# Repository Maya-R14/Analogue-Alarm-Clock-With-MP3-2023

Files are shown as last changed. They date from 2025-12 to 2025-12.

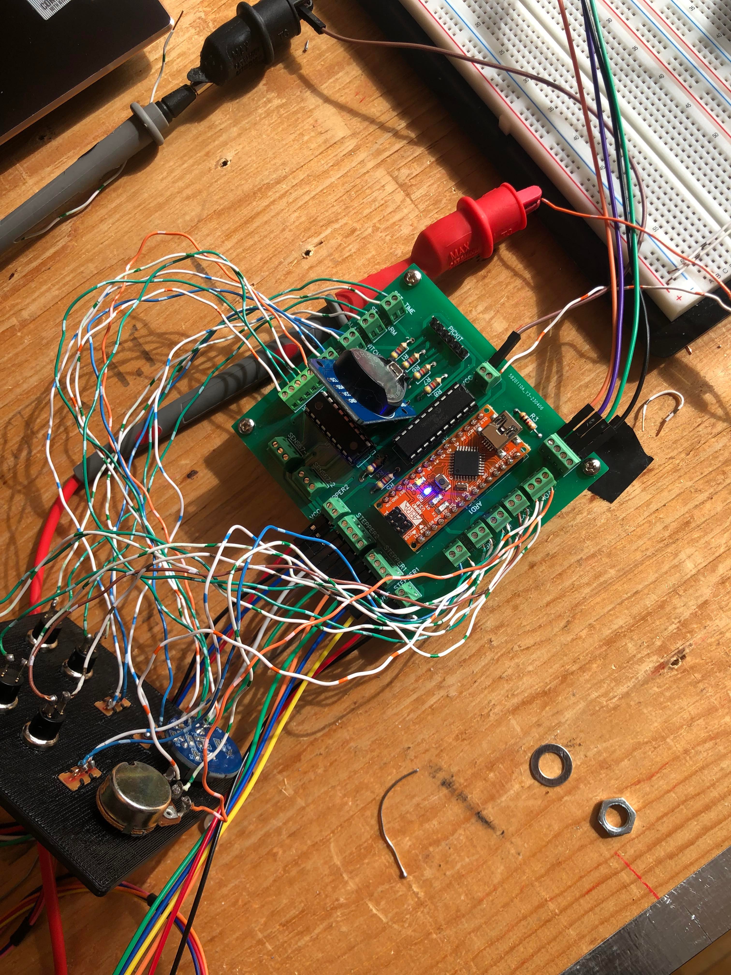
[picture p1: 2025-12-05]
Media/Testing with PCB.jpg

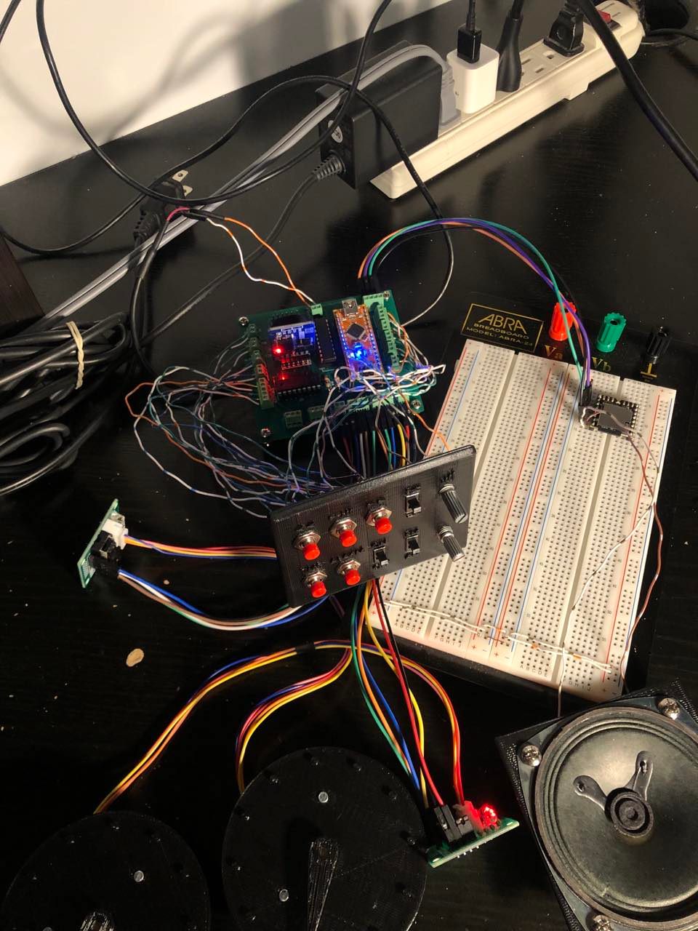
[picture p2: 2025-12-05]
Media/Testing with PCB and Faceplate.jpg

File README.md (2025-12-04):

# Analogue-Alarm-Clock-With-MP3-2023
An analog clock driven by DC motors, integrated with an MP3 playback module, combining mechanical control and embedded electronics.

## Features
- DC motor–driven clock hands for precise movement
- Integrated MP3 module for alarms or notifications
- Custom PCB for motor and module integration

## Hardware
- DC motors for clock hands
- MP3 module
- RTC module (I2C Communication)
- Microcontroller (PIC and Arduino)
- Motor drivers
- Speaker
- PCB, resistors, capacitors

## Software / Tools
- Arduino IDE (C/C++)
- DipTrace
- Salea Logic 2
- 3D Printing/Solidworks
- Laser Engraver

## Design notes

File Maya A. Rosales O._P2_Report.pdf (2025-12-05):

John Abbott College

Engineering Technologies Department

Name/Team Names:

Maya A. Rosales O.

Project 2

Technical Report

Title: Analog Clock with MP3 Player

Instructor: Hana Chammas

Date: May 27, 2023

Winter 2023

## Contents

Introduction___________________________________________________________________2

Problem Description____________________________________________________________2

Proposed Solution______________________________________________________________2

Product Development___________________________________________________________3

Technical Product Description___________________________________________________10

Operation______________________________________________________________10

Maintenance___________________________________________________________11

Troubleshooting________________________________________________________12

Lessons Learned______________________________________________________________ 13

Final OPPM_________________________________________________________________ 14

References___________________________________________________________________15

Acknowledgement and Credits___________________________________________________15

Appendix____________________________________________________________________15

A1. Bill of Materials_____________________________________________________15

A2. Media_____________________________________________________________16

A3. Engineering and Manufacturing Documentation____________________________17

A4. Miscellaneous_______________________________________________________17

## Introduction

For my project 2, I set out to build an analog clock that plays music. In this document, I will go into lengthy detail about the problem that I was trying to solve, the solution I came up with, and the steps I took to reach that solution.

I also describe in detail the process of building the clock, along with how to use it.

I wanted the clock to be aesthetically pleasing and intuitive to use and this is a philosophy I kept in mind while working on my project.

All the relevant files along with the bill of materials are also available in the index section of this document.

I would like to thank Nic the technician once again for all his help and support while working on this project.

## Problem Description

With modern phones, most people have alarms at the palm of their hands, the issue with this is that phones can fail for a number or reasons. It can range from simply forgetting to charge one’s battery, to it getting stolen, software malfunction, busted speak, etc. Having a separate dedicated time keeping/alarm device would allow for a better peace of mind and could make nice décor piece, enhancing the appearance of a room.

Most people are also woken up by blaring and disruptive alarm sounds. Although this does the job, it is rather unpleasant and, wouldn’t a person prefer to wake up to the sound of their favorite song?

## Proposed Solution

My proposal is to build an analog clock so that a user can upload their own tracks to play when the alarm goes off. The tracks will play in either a predefined sequence or at random, as selected by the user via an interface on the analog clock.

The reason it’s analog as opposed to digital is that analog adds a certain aesthetic element to the project that a digital clock doesn’t.

Alternatives:

Radio alarms have been around for a very long time, although this doesn’t allow the user to choose the music being played.

There are also light alarms, which instead of playing a sound, will use a light source to attempt to wake up the person. This is an interesting alternative, as most of these alarms claim to have health benefits over regular sound alarms. The issue with this is that the science behind it remains contentious as best. Not only that, but most of these alarms can be rather expensive.

The pros and cons of using a phone have been discussed in the previous section.

## Product Development

From the beginning, the idea was to create two separate systems for the clock, the “clock”, which would be handled by the PIC16F690 and the MP3 Player, which would be handled by an Arduino. The idea of creating two separate systems instead of one was so that they could operate independent of each other. This allows the user to listen to music using the MP3 player without disrupting the clock functionalities. Each microcontroller can “focus” on what it’s good at.

After this, I moved on to the electrical and mechanical aspect of the clock. For the electrical, I designed a schematic and PCB board using Diptrace. I then converted the PCB into Gerber files which I then sent to JLCPCB to print into a board.

The mechanical aspect involved 3D modeling the gear system and the case. After this was done, pieces were 3D printed and assembled. The front plate and the needles were laser cut and engraved.

Clock & Alarm

I’d like to preface by saying that a huge chunk of the time dedicated to this project was spent coding the PIC16F690. This is because no relevant libraries of code were readily available. Therefore, all the code for the clock and alarm was written from scratch.

With the understanding that two stepper motors would be used to move the needles, a rotary encoder to control the motors, an RTC module to keep track of the time and a handful of switches and buttons as UI, these components were bought from the very beginning, allowing for prototyping to begin.

Very early in development, it was made very obvious that the microchip did not have enough pins for all the I/O’s that were required. This prompted the purchase of the MCP23008 I/O port expander.

The code works as follows:

On power up, the microcontroller will enable all the ports as inputs, enable I2C communication, turn the alarm off (if the alarm switch is on, the alarm will be turned on anyways) and move the hands to the 0 position.

The first think the code does once it has been initialized is to check if any buttons have been pressed. The “Buttons()” function is called, which checks if the Time button, Alarm button or Alarm switch have been toggled.

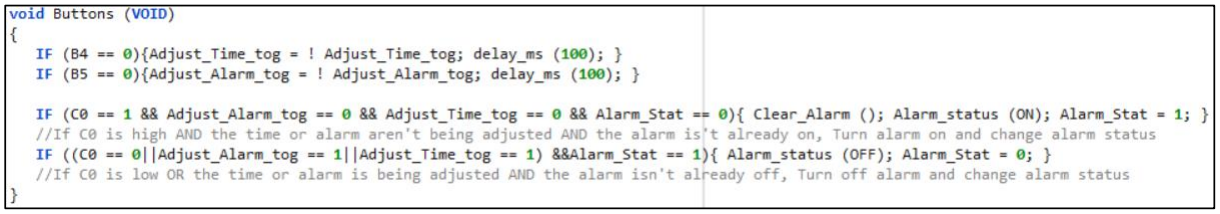
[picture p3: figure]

Once this is done, the code has three branches. Adjust time, Adjust Alarm and Display time. Since, in theory, the DS3231 already has the proper time stored, the clock will initialize on “Display time mode.”

Display time

The display time function
first fetches the time
(minutes) from the DS3231
and stores the value in
Time_min. Minutes are then converted to steps and the stepper is moved into
positions. Although the
stepper requires 2048 steps to make a full rotation,
Minutes advance in 34 steps increments (60 mins = 2040 steps). This is because the microcontroller is unable to handle decimals and to get a an exact 2048, each min
would have to be 34.13333
steps. To compensate for
this the last step has an
additional 8 steps.

The hours needle works in a

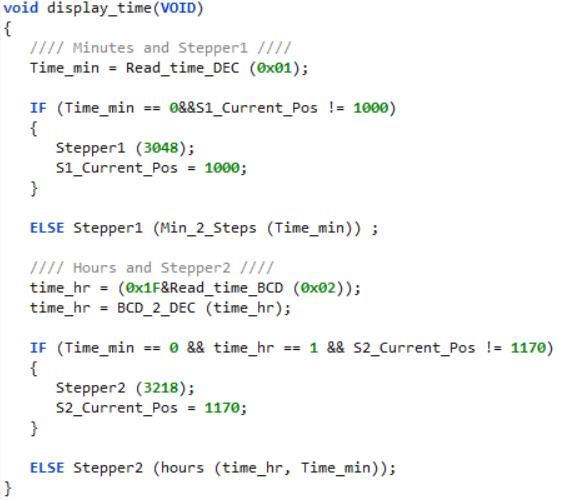
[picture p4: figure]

similar manner. It fetches the time (hours) from the DS2321 and stores the value into Time_hr. It masks the first 3 bits as they contain information that is not relevant and then converts it into decimal. Hours increase in 170 step increments. The hours needle also moves slightly closer to the next hour as minutes increase. This is done to simulate an analog clock. For every 6 mins, the clock will move 17 steps. Once again, the hour of the clock has an additional 8 steps to compensate.

Adjust time

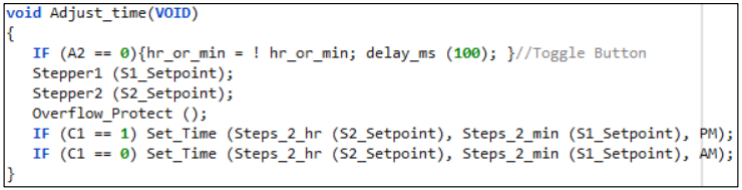
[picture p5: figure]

The adjust time function first enables interrupts to allow control of the motors through the rotary encoder. After this, it will check if the built in button on the rotary encoder has been pressed. This button allows the user to toggle between motors. After this, the two steppers will be moved into the new position.

The “Overflow_Protect” function serves to keep the position value of the motors within the expected range. The code is designed under the assumption that motor is within 0-2048 steps. If the motor is outside this range, it will replace the position value with an equivalent position value. If the motor goes to step 2148, It will move to position 2148 and replace the position with 100 (2148 - 2048 = 100).

Finally, the new position will be converted into time and the DS3231 will be updated. Whether the time is AM or PM is determined by the position of the AM/PM switch.

Adjust Alarm

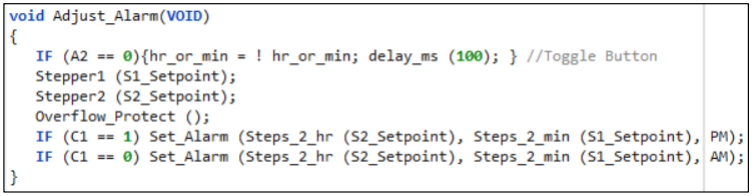
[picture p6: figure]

The adjust alarm function operates the same the adjust time function does, but instead of updating the time register in the DS3231, it updates its alarm register.

Lastly, the code will check if the alarm has gone off and if so, it will clear the alarm to allow for the next time I needs to go off.

The main function looks as shown bellow, the full code along with the relevant header files are available in the manufacturing section of this document.

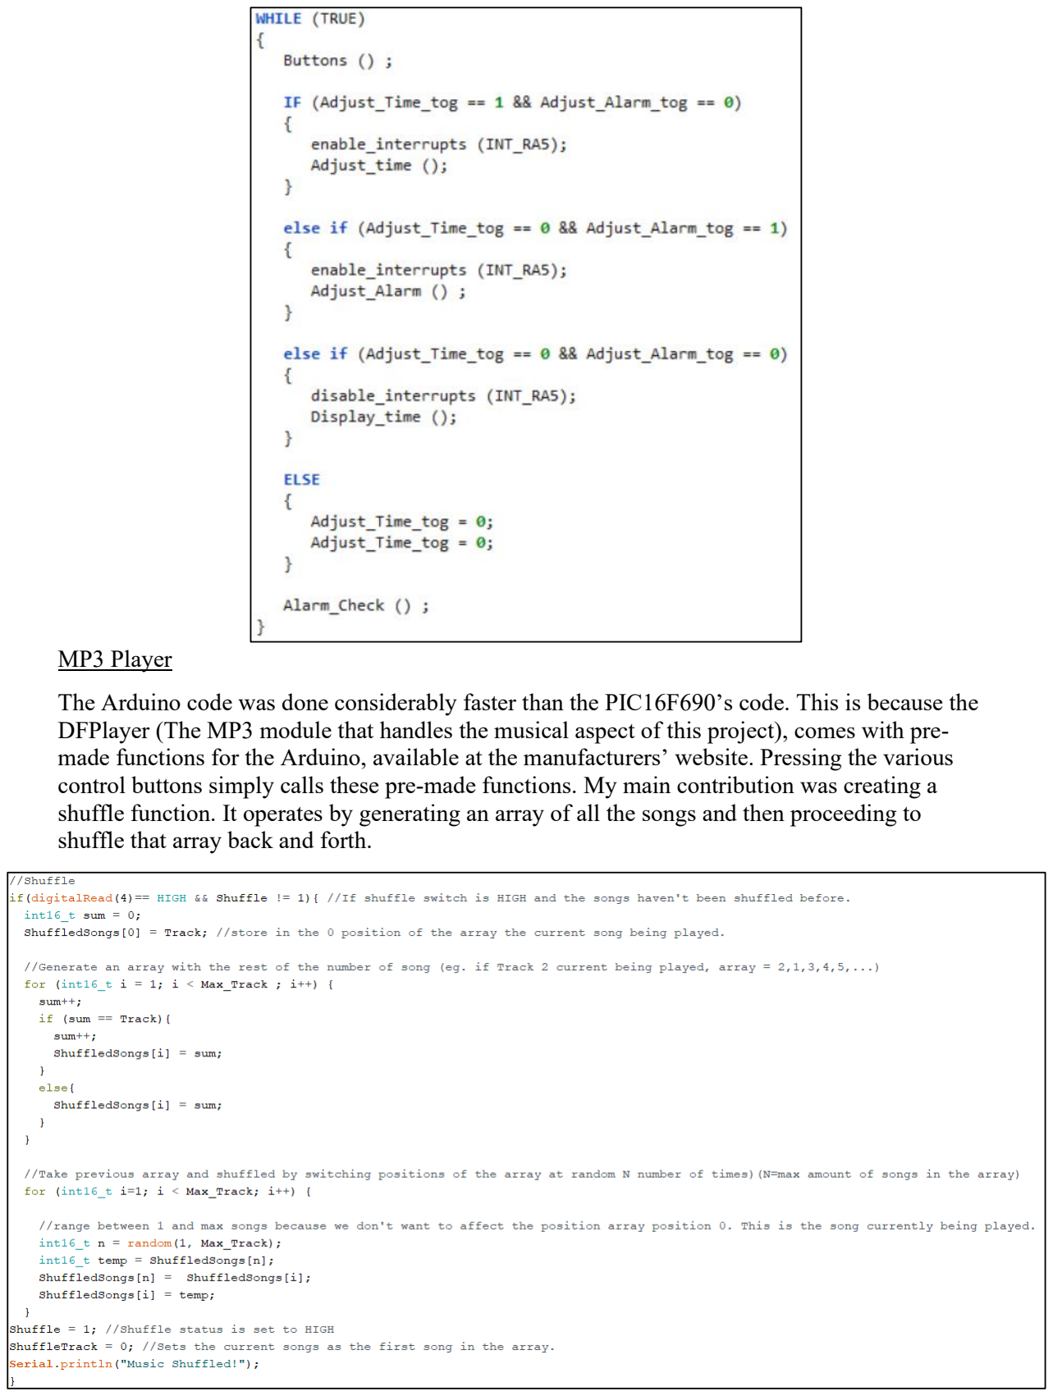
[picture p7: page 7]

MP3 Player

The Arduino code was done considerably faster than the PIC16F690’s code. This is because the DFPlayer (The MP3 module that handles the musical aspect of this project), comes with pre-made functions for the Arduino, available at the manufacturers’ website. Pressing the various control buttons simply calls these pre-made functions. My main contribution was creating a shuffle function. It operates by generating an array of all the songs and then proceeding to shuffle that array back and forth.

Schematics and Board

After fully coding the project and having a working prototype, I moved on to creating a compact PCB board for all the components. Although the electrical aspect of this project is not exceedingly complex, creating a schematic and a board is still crucial as there are several connections on the board and multiple inputs and outputs. Attempting to create a simple board from a prototype PCB would be excruciatingly hard. This is why once I had a schematic and a PCB board design, I sent it out to print with JLCPCB. The schematic and the PCB are as shown bellow and the files are available in the manufacturing section of this document.

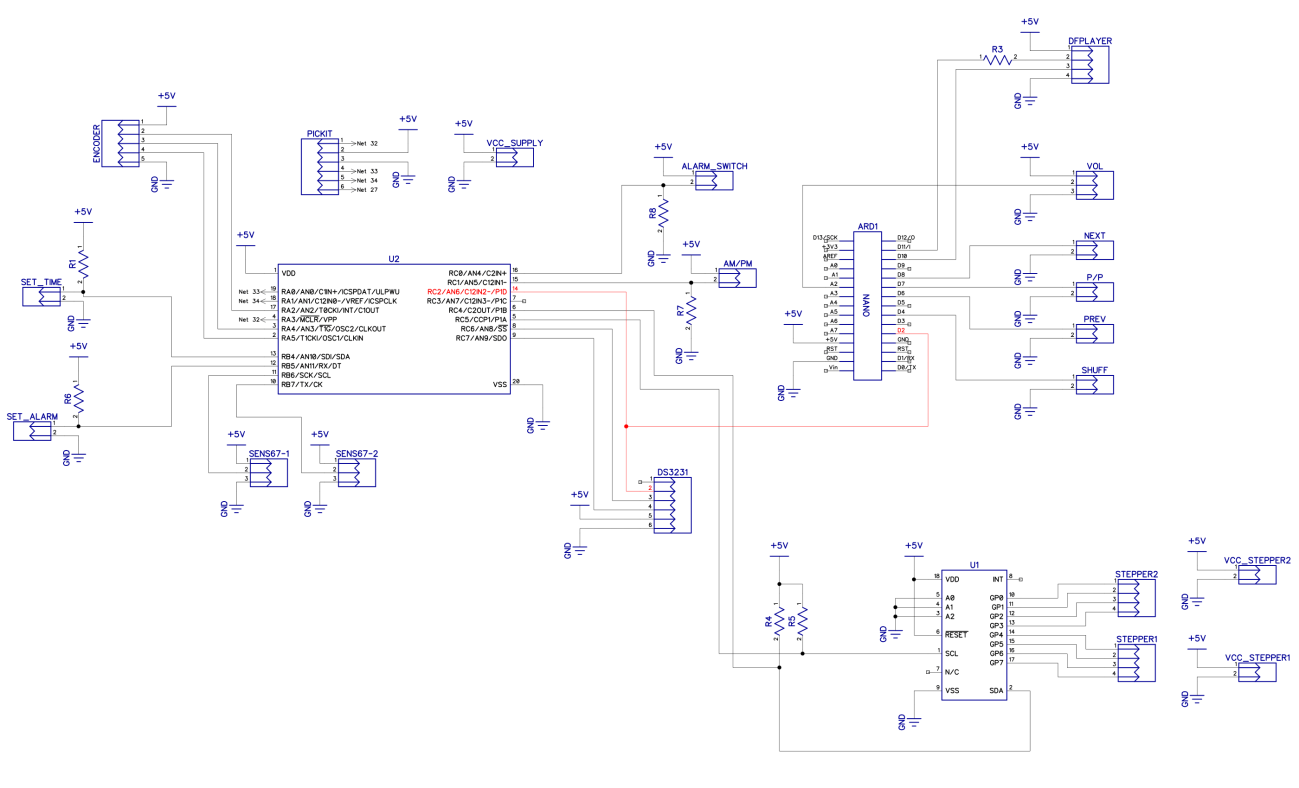
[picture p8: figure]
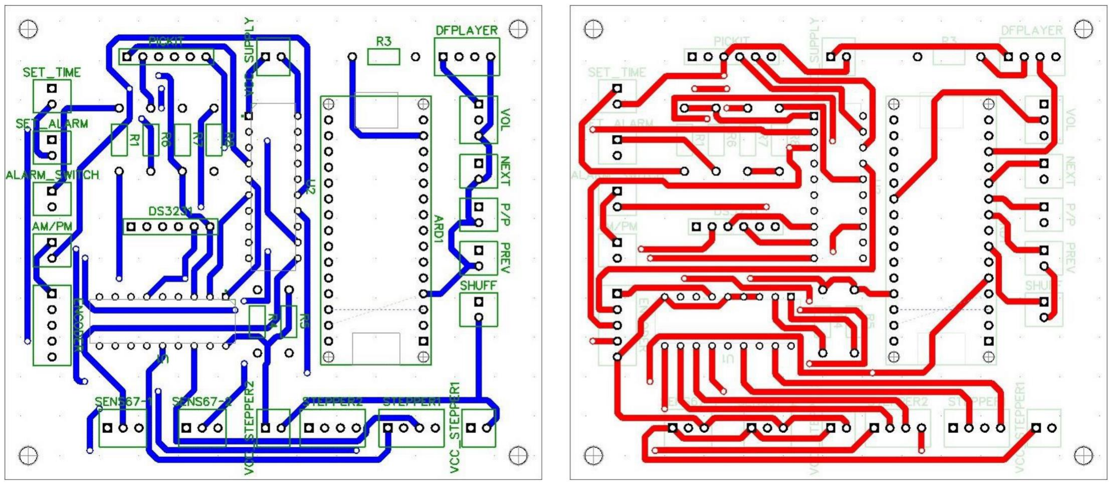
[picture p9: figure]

Gearbox

After handling the software and electrical aspects of the project. The mechanical aspect came into focus. Clocks generally have concentric shafts. Each one controlling a single needle. The goal was to recreate this system using the motors that I had in hand. The “gearbox” as shown bellow was conceived.

Each gear has 32 teeth. 32 being a divisor of 2048 which is the total amount of steps for a full revolution.

On both of the gears that function as shafts, there is a small whole near the edge of the gear. Inside this whole there’s a magnet glued. This is because there is a hall sensor module that hovers slightly above the gear. This sensor is used to determine the house position of the needles. On power up, the gears will rotate CCW until the magnet is detected and the home position is reached.

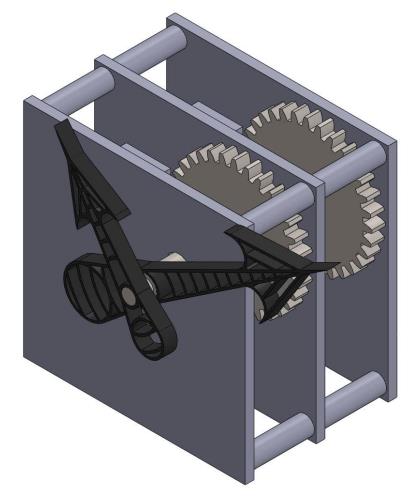
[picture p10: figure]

Case

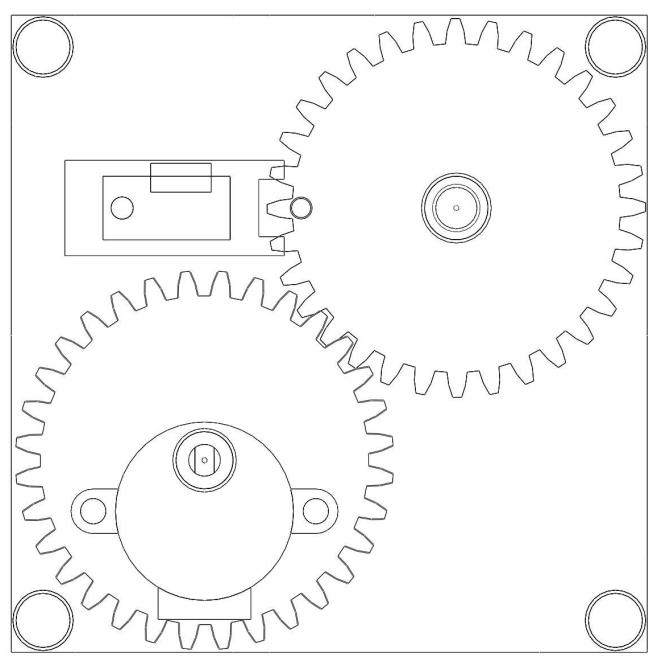
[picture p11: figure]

After this, the design of the case was rather simple. It simply had to be designed to fit the components and the gear box at the same time. Having a 3D model made of solid works with all the necessary references took out all the guesswork from this. The final look of the case is as shown bellow. Although because of its size, it had to be printed in two parts and then glued together. The face plate and the needles were then laser cut and engraved at the Pierrefonds library.

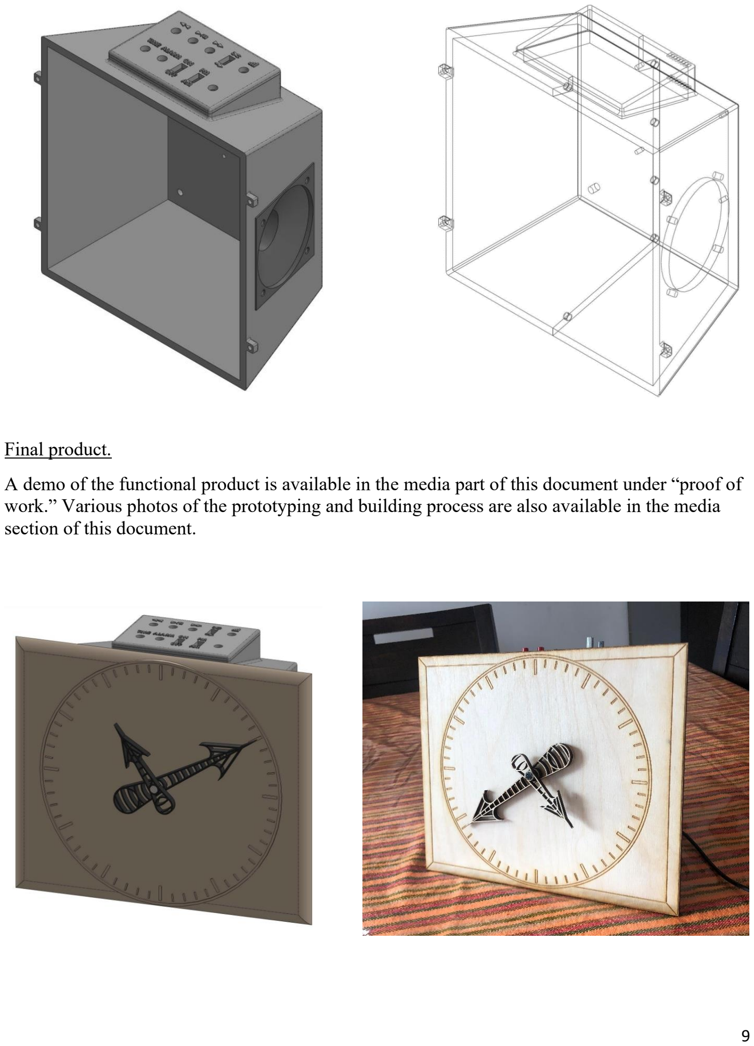
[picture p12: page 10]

Final product.

A demo of the functional product is available in the media part of this document under “proof of work.” Various photos of the prototyping and building process are also available in the media section of this document.

## Technical Product Description

## Operation

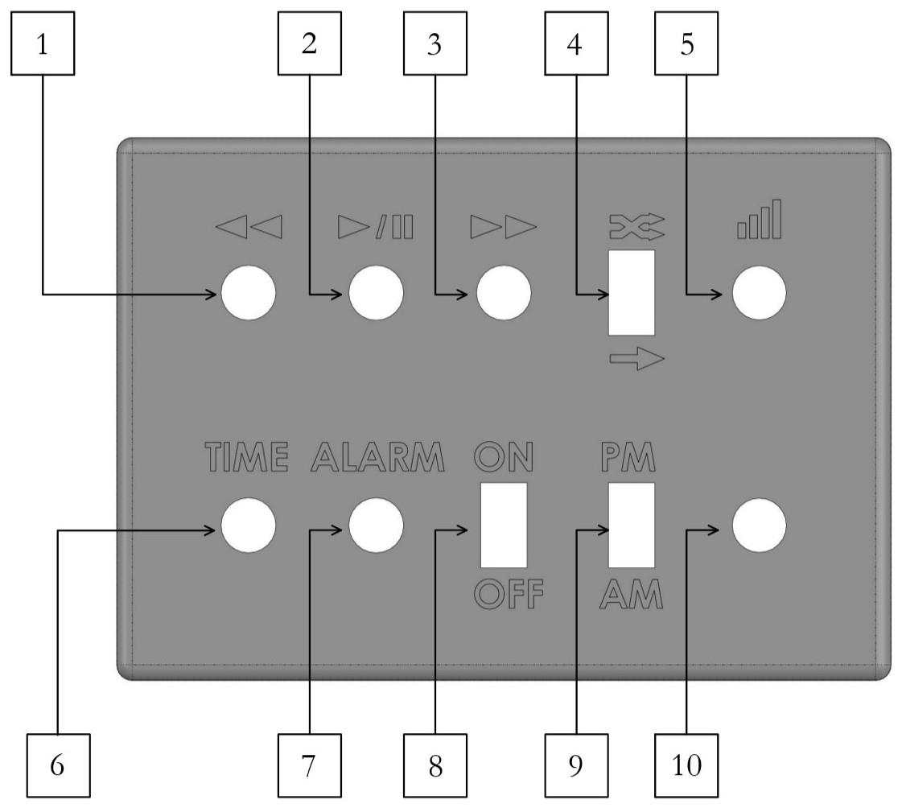
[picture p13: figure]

1 | Previous Button Pushing this button plays the previous song on the queue. | 6 | Set Time Button Pushing this button allows you to set the time using the AM/PM switch and the control knob.
2 | Pause Button Pushing this button will pause the song currently playing. Pressing it again resumes it. | 7 | Set Alarm Button Pushing this button allows you to set the alarm using the AM/PM switch and the control knob.

3 | Next Button Pushing this button plays the next song on the queue | 8 | Alarm Switch The alarm switch is used to turn the alarm on and off.
4 | Shuffle Switch When the switch is on the shuffle position, all the songs inside of the SD card will be shuffled. If not, they will play in the order in which they are stored. When the alarm goes off, if the switch is in the shuffle position, it will play a song at random. If not, it will play the first song stored in the SD card. | 9 | AM/PM Switch As the clock only has 12h and the day has 24, the AM and PM switch helps the clock differentiate between before noon and after noon, whenever the user is setting the time or the alarm.
5 | Volume Control Knob Turning the knob CW will increase the volume. Turning it CCW will decrease it. | 10 | Clock Control Knob The control knob is used to move the needles and set the time when changing the time or the alarm. The knob also functions as a button. Pushing it down will toggle control between the two needles.

MP3 Module

The MP3 module at the back of the control panel is for micro-SD cards. When plugging in the clock for the first time, an SD card ought to be inserted for the MP3 module to properly initialize.

Inside of the SD card, there needs to be a folder labeled as “MP3”, this is where songs should be stored for the module to recognize them.

The file names need to be formatted as follows:

0001 songtitle1
0002 songtitle2
0003 songtitle3
…

The module is able to handle up to 500 songs.

## Maintenance

Inside of the clock, there is a DS3231 RTC module equipped with a LIR2032. This battery is what allows the clock to keep track of the time even when it isn’t powered. This battery should be replaced once every 10 years. It is important to know that one should NOT replace this battery with the more widely available CR2032. Doing so will make the battery expand.

An expanded battery is a fire and explosive hazard.

The clock should also not be stored in humid environments or direct sunlight. Direct sunlight may cause the PLA to shrink, warm and eventually crack. Humid environments may damage the wood face plate and the needles.

## Troubleshooting

The internal machinery of the clock can be easily accessed by removing the four screws at the back of the face plate. Here are some simple troubleshooting steps for common issues. If any other issues arise, please contact the manufacturer for further assistance.

Rattling Noise at Loud Volumes

If there seems to be rattling noises at high volumes, it may be because the wires to the control panel are in contact with the back of the speaker. This causes the wires to rattle and make a noise at high volumes. The solution is simply to open the clock and shift the cables away from the speaker.

Clock Out of Phase

If the clock seems to be displaying the wrong time or is out of phase, simply unplug and plug back in the clock. The home position is reset on power up every time, so this ought to fix the issue, if not the home position might be out of phase.

Home Position out of Phase.

If the home position is out of phase, it is because the hall sensors that are used to set the home position have been tampered with. To fix this, simply access the inside of the clock. The gearbox will be attached to the back of the faceplate. Inside of the gearbox, there will be two red modules directly above the gears. To fix this issue, simply push the sensors back into position. Pushing the sensors CW will shift the home position CCW. Pushing the sensors CCW will shift the home position CW.

Clock Does Not Update Time On Power up

The clock is equipped with a module that allows it to keep track of the time even when it is disconnected. This allows the clock to auto set the time when powered on. If this is not the case, the battery might have died, consult the maintenance section of this document for further details.

MP3 Not Working

The MP3 will enter a “locked” state if the clock is initially powered without an SD card inserted. Try to unplug, insert an SD card, and plug in the device again. You should see the blue LED of the module flash once. For any other issues with the MP3 module, consult the operation section in this document.

## Lessons Learned

I have learned about the advantages and disadvantages of different manufacturing processes.

For the most part, I have stuck with 3D printing when it comes to building my projects. This is because 3D printing is accessible, relatively fast, and easy. In this project, I had the chance to work with a CNC engraving machine and it opened my eyes to new possibilities. CNC machines are simply much more precise than 3D printers. They also don’t face the same limitations of wrapping and shrinkage. If given the chance to do it again, I would probably redo the gears with a CNC machine. The printed gears currently implemented have barely passable clearances. CNC would allow the gears to make more precise motions, making the clock more precise.

I also learned the hard way that PLA is a lot more susceptible to warping than I thought. I spray painted a piece and left it outside to dry. When I came back, the piece was warped.

3D printing still has its place though. I would not have been able to manufacture some of the more complex pieces through CNC. The shape of the case required the piece to be 3D printed.

Regarding project planning, I’ve learned that all project development loosely follows the same steps. Design. Prototype. Test. Rinse and repeat, until the project is complete.

## Final OPPM

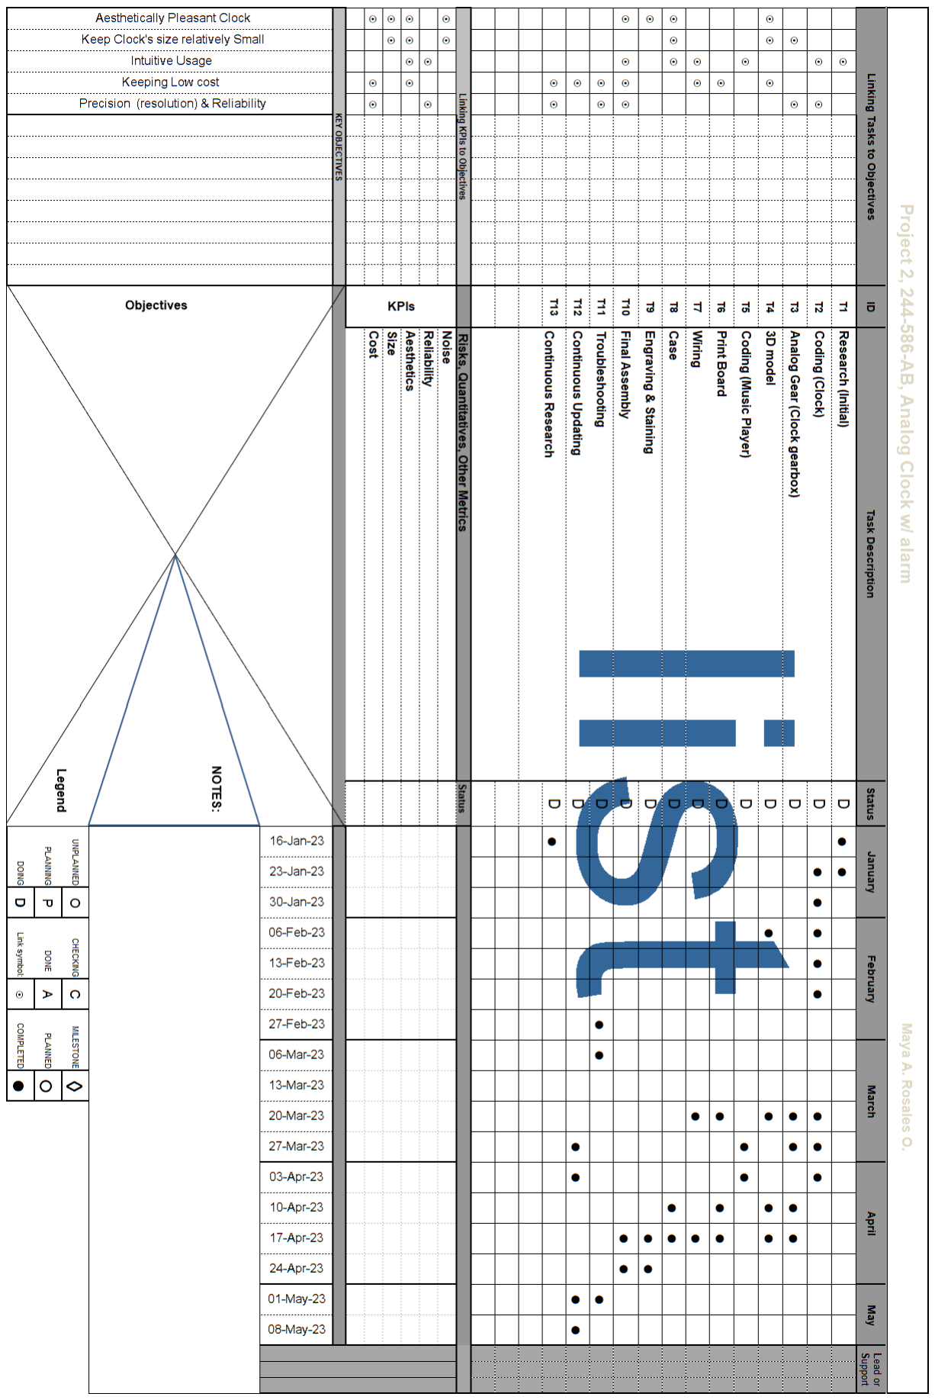
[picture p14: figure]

## References

[1]
“PIC16F690,” Microchip.com, 2023. https://www.microchip.com/en-us/product/PIC16F690 (accessed May 17, 2023).

[2]
“MCP23008,” Microchip.com, 2023. https://www.microchip.com/en-us/product/MCP23008 (accessed May 17, 2023).

[3]
Adafruit Industries, “Adafruit DS3231 Precision RTC Breakout,” Adafruit.com, 2016. https://www.adafruit.com/product/3013 (accessed May 17, 2023).

[4]
“Nano | Arduino Documentation,” Arduino.cc, 2023. https://docs.arduino.cc/hardware/nano
(accessed May 17, 2023).

[5]
“DFPlayer Mini Mp3 Player - DFRobot Wiki,” Dfrobot.com, 2016. https://wiki.dfrobot.com/DFPlayer_Mini_SKU_DFR0299 (accessed May 17, 2023).

## Acknowledgement and Credits

I’d like to thank Nic the technician for providing components/replacements when needed, opening the workshop early in the morning and for his never-ending patience.

## Appendix

## A1. Bill of Materials

# | Name of Product | Part # | Quantity | Unity Cost | Cost

1 | Stepper Motor (With Driver Board) | MOT-28BYJ48 | 2 | $ 6.95 | $ 13.90
2 | PIC Microcontroller | PIC16F690-I/P | 1 | $ 4.54 | $ 4.54
3 | RTC Module | ARD-DS3231 | 1 | $ 8.79 | $ 8.79
4 | Rotary Encoder | SW-ENC-03 | 1 | $ 4.38 | $ 4.38
5 | Arduino Nano Board | ABRANANO | 1 | $ 19.45 | $ 19.45
6 | Magnetic Hall Effect Sensor | SENS-67 | 2 | $ 2.79 | $ 5.58
7 | DFPlayer - MP3 Player Module | DFR0299 | 1 | $ 15.31 | $ 15.31
8 | Round Magnets 3x3mm (20 Pack) | MAG-N-03 | 1 | $ 2.41 | $ 2.41
9 | Speaker - 4ohms 3 Watts | 1314-ADA | 1 | $ 3.76 | $ 3.76
10 | IC Socket 18 Pin | 18LP | 1 | $ 0.15 | $ 0.15

11 | IC Socket 20 Pin | 20LP | 1 | $ 0.16 | $ 0.16
12 | Slide Switch SPDT | SSW-110 | 3 | $ 0.60 | $ 1.80
13 | Normal Open - Push Button | NO-112RD | 5 | $ 1.20 | $ 6.00
14 | 40 Pin Header | FH-1 | 1 | $ 1.07 | $ 1.07
15 | 2-Pin Terminal Block, 4 Pack | 2491P | 3 | $ 3.46 | $ 10.38
16 | 3-Pin Terminal Block, 3 Pack | 2492P | 1 | $ 3.84 | $ 3.84
17 | 4-Pin Terminal Block, 2 Pack | 2493P | 2 | $ 3.46 | $ 6.92
18 | 5-Pin Terminal Block, 2 Pack | 2494P | 1 | $ 4.23 | $ 4.23
19 | PCB | Y3 | 1 | $ 18.38 | $ 18.38
| | | | Subtotal | $ 131.05
| | | | Total | $ 150.71

Sources along with links and receipts are provided in the BOM excel sheet provided along with this document.

Most of the pieces mentioned above were obtained through ABRA Electronics.

## A2. Media

Reference Number | Link | Description
1 | Prototyping (Clock).jpg (https://johnabbott-my.sharepoint.com/:i:/g/personal/hana_chammas_johnabbott_qc_ca/EfyJBlQJfkpGrinnBd8_jHUBXoqIFZfPf4KDeW7__75n8A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) | Prototyping & coding the clock with the PIC 16F690.
2 | Prototyping MP3.jpg (https://johnabbott-my.sharepoint.com/:i:/g/personal/hana_chammas_johnabbott_qc_ca/ERP7IIV5siZLrGnSnSNXnykBqrb-URET-D5xRm33PmA8LQ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) | Prototyping & coding the MP3 with the Arduino and the DFPplayer.
3 | PCB Board.jpg (https://johnabbott-my.sharepoint.com/:i:/g/personal/hana_chammas_johnabbott_qc_ca/Ef6ZnLtAUl5IrvlFOkLV4PMBv0wRerk8gTF7JCkFm1GyTw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) | PCB Board as delivered by JLCPCB.
4 | PCB Board Populated.jpg (https://johnabbott-my.sharepoint.com/:i:/g/personal/hana_chammas_johnabbott_qc_ca/ERpo0wbm8NVMuVTVmTrUdmcBYysfo8PYaHdZnyQgHFdnRA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) | PCB Board with component soldered on.
5 | 3D Clock.png (https://johnabbott-my.sharepoint.com/:i:/g/personal/hana_chammas_johnabbott_qc_ca/Ea2wddwp81BDlBsna88hI4QBzvU_FcoxmpR8pZIl2xiorw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) | 3D Model of the clock. Model is an Assembly in Solidworks.
6 | Testing with PCB.jpg (https://johnabbott-my.sharepoint.com/:i:/g/personal/hana_chammas_johnabbott_qc_ca/ERz7X7GkU9ROq41NsKTRgBIB8-55I6dhdhe9wsHhaLHJ1w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) | Testing the PCB Board with the faceplate.
7 | Testing with PCB 2.jpg (https://johnabbott-my.sharepoint.com/:i:/g/personal/hana_chammas_johnabbott_qc_ca/EVWLNjiqD_hFlJIHQGTORIUBVftSHUYuwHwyhvL64R-T-g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) | Testing the PCB Board with the faceplate.
8 | Gearbox.jpg (https://johnabbott-my.sharepoint.com/:i:/g/personal/hana_chammas_johnabbott_qc_ca/EWCcGIzLmwBPoC_3terp4NgBD7hLLJUuqkpptupk_vZDRg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) | 3D Printing and Assembling the gearbox of the clock.
9 | Clock Without Faceplate.jpg (https://johnabbott-my.sharepoint.com/:i:/g/personal/hana_chammas_johnabbott_qc_ca/EeKShwr4swZKmXg9szsZDUAB7Si2etoA1Wc0r1ALOMUS2g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) | 3D Printing and Assembling the clock. Without faceplate.
10 | Final Product.jpg (https://johnabbott-my.sharepoint.com/:i:/g/personal/hana_chammas_johnabbott_qc_ca/ETpjvZY75ShJhAzZesAumNMBTCt9Rs6OquvOULI_QOuw9A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) | Final Product fully assembled.
11 | Proof of work.mp4 (https://johnabbott-my.sharepoint.com/:v:/g/personal/hana_chammas_johnabbott_qc_ca/EYqeKdWGFHFMhp2PoWl4e4IByUH11_62dSp0aFdoKYJr7w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) | Proof of final product working.

## A3. Engineering and Manufacturing Documentation

## A4. Miscellaneous

N/a

Reference Letter | Link | Description
A | Time & Alarm (PIC16F690) (https://johnabbott-my.sharepoint.com/:f:/g/personal/hana_chammas_johnabbott_qc_ca/EvvLlzc9fVFBpA5Ho4jv7uMBD7Osuf98Mkvgk36m6ha2vQ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) | Code - PIC16F690
B | MP3_Play_Arduino (https://johnabbott-my.sharepoint.com/:f:/g/personal/hana_chammas_johnabbott_qc_ca/EgXJXToQIc9HpTtF2U_msuABqa_6zQZqDUF3O0t6PKwAnQ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) | Code - Arduino
C | Clock Parts & Assembly (https://johnabbott-my.sharepoint.com/:f:/g/personal/hana_chammas_johnabbott_qc_ca/Eif_Ptz6X-VLnYx6wWqHHBQB53J0yem2S5YLc0GMDiZtNw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) | 3D Model - Parts & Assembly
D | Maya A. Rosales O._P2_Drawings_FULL.pdf (https://johnabbott-my.sharepoint.com/:b:/g/personal/hana_chammas_johnabbott_qc_ca/EUlfz-RqdBJJioLE9KqUQWIBjBCIqAZp4ldYz9ki7Yr15A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) | 3D Model - Drawings - PDF
E | 3D Printing Files (https://johnabbott-my.sharepoint.com/:f:/g/personal/hana_chammas_johnabbott_qc_ca/EtBzCASFOX5MiRp3lxm5brYBV6-8efRSfK99PAzaBy-odQ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) | 3D Model - STL Files
F | CNC Files (https://johnabbott-my.sharepoint.com/:f:/g/personal/hana_chammas_johnabbott_qc_ca/EpIzLJuC2exFr5EQcHanLccBuOppXHOZoq5Oobz83oYafQ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) | 3D Model - DXF Files
G | PCB.dch (https://johnabbott-my.sharepoint.com/:u:/g/personal/hana_chammas_johnabbott_qc_ca/EYTdmmJZivVGiBz0uwGeaxsBYo_vE_yDKNbHGOmHrR4ccA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) | PCB - Schematic
H | Pattern Files (https://johnabbott-my.sharepoint.com/:f:/g/personal/hana_chammas_johnabbott_qc_ca/ErarjGPN741Ota4kyVBdPmcBJLAJBGpTxW95eY8gZa_whw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) | PCB - Pattern Files
I | PCB.dip (https://johnabbott-my.sharepoint.com/:u:/g/personal/hana_chammas_johnabbott_qc_ca/ESxMsjZzhSBDoRBxHmN3lZUByvFgZZd7ztYUkvlAaRMLXw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) | PCB - Board
J | PCB_gerberx2_Y3.zip (https://johnabbott-my.sharepoint.com/:u:/g/personal/hana_chammas_johnabbott_qc_ca/ETHW3v9lWM5Fm1W8BO8L7FkBOjD2WB_BM08k5GUc-o0Tew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) | PCB - Gerber Files

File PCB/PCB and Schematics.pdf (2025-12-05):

SCHEMATICS

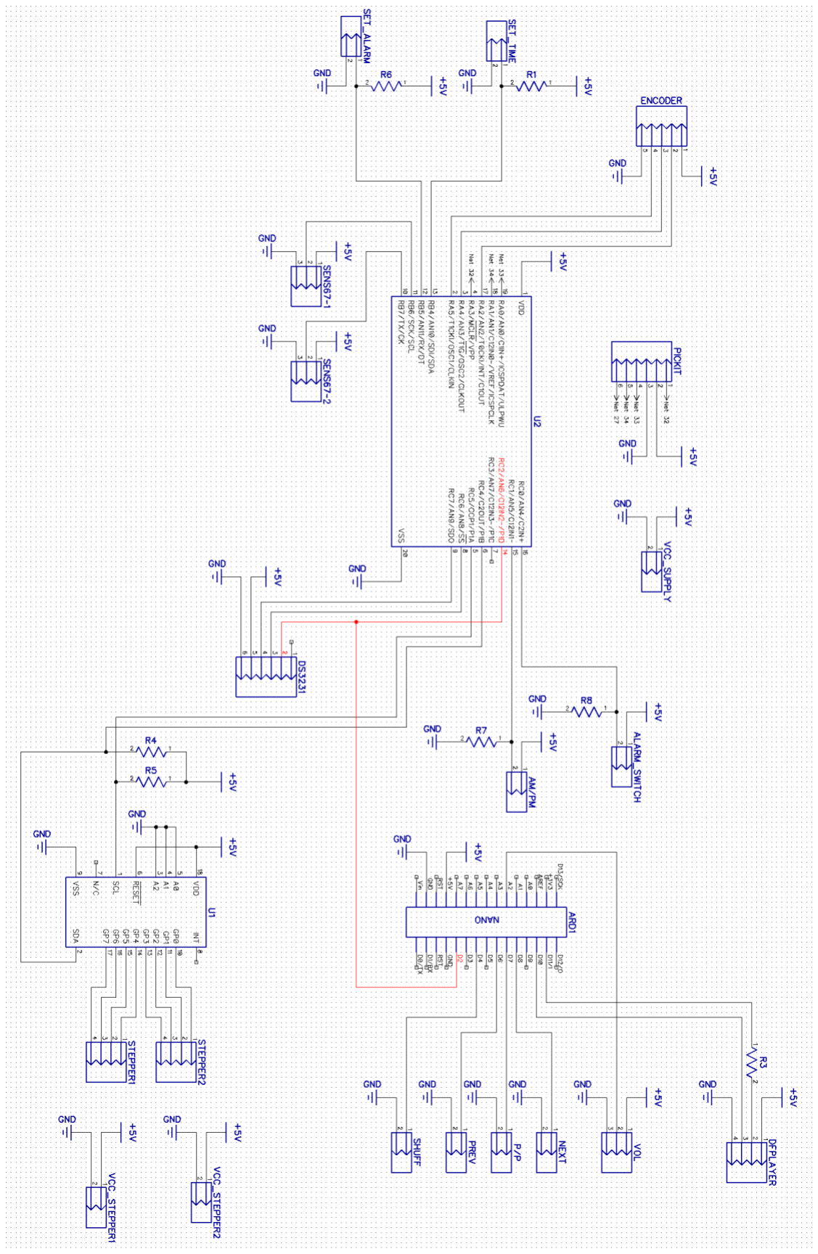
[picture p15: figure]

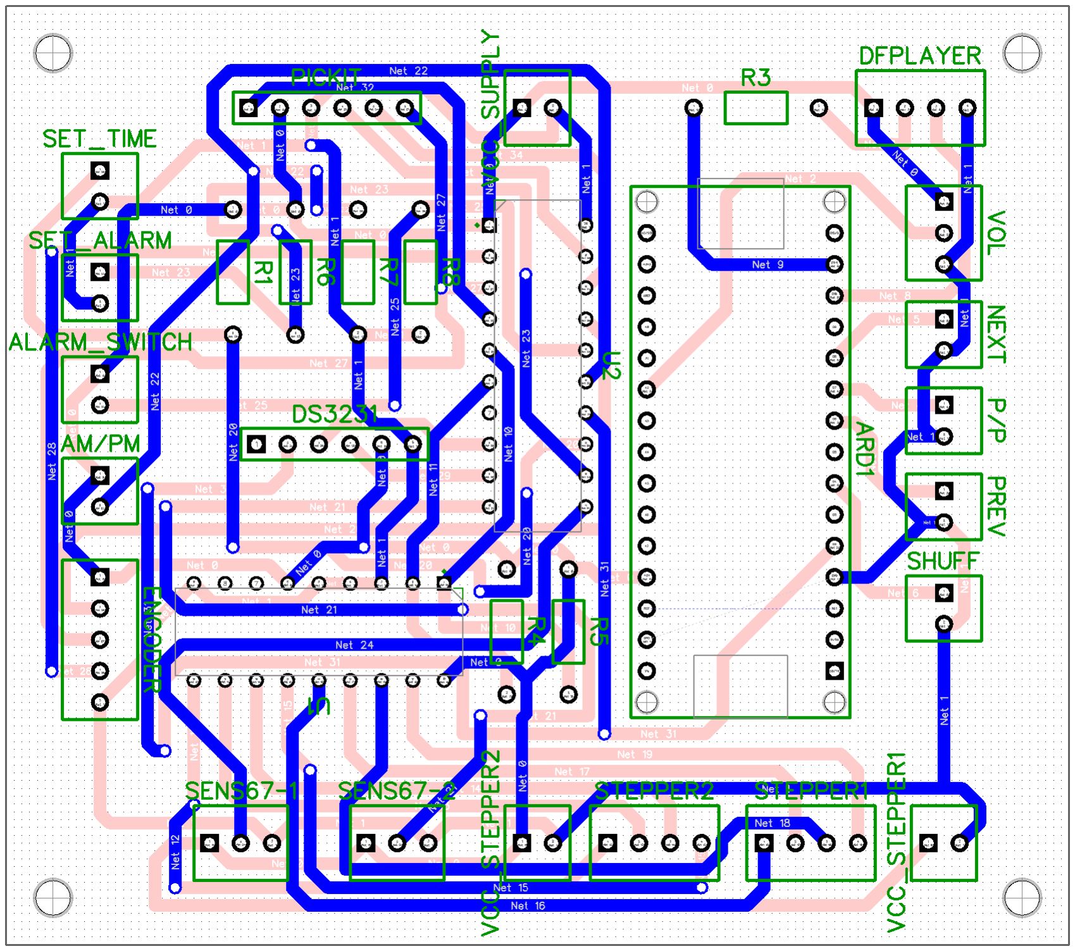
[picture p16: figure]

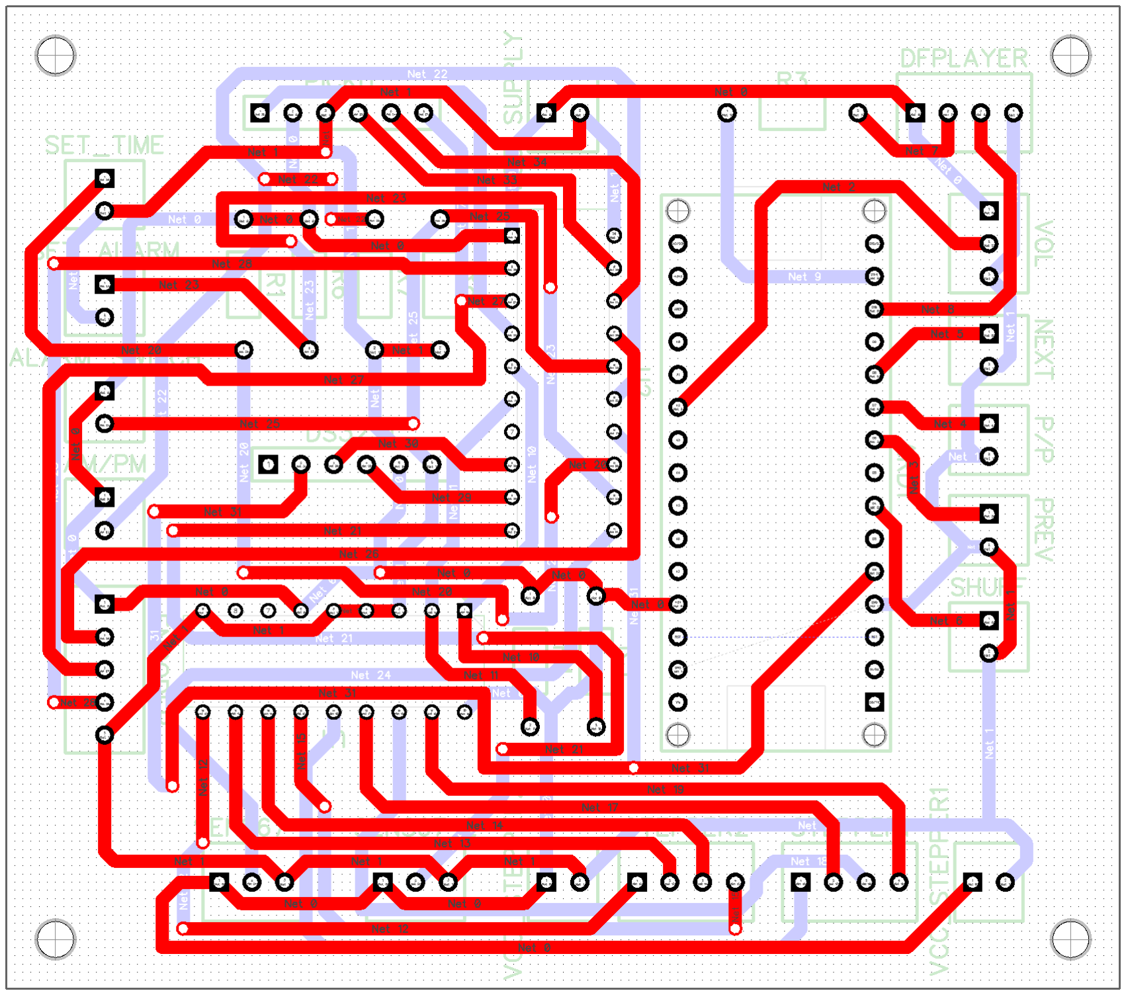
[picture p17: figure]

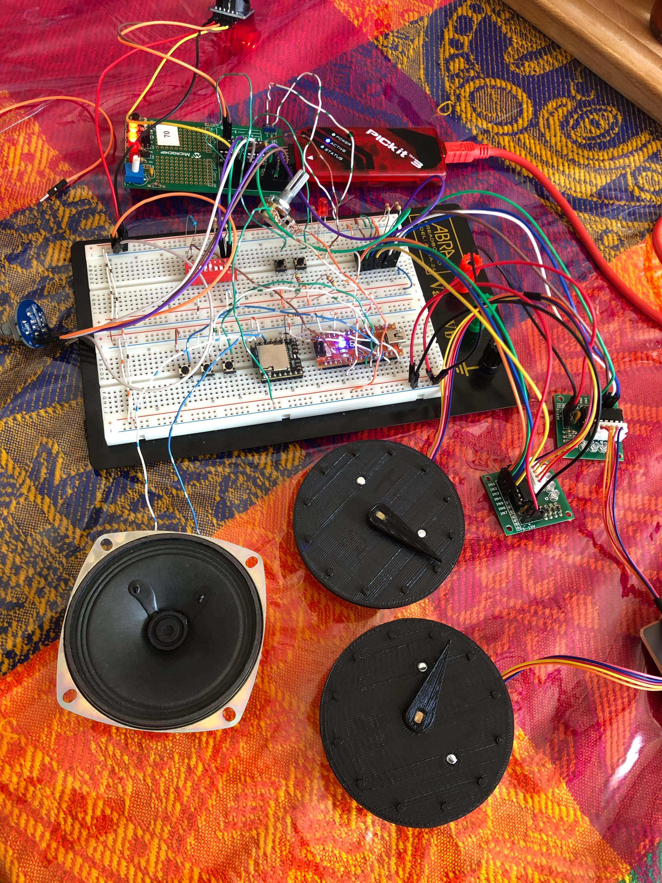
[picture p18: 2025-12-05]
Media/Prototyping MP3.jpg

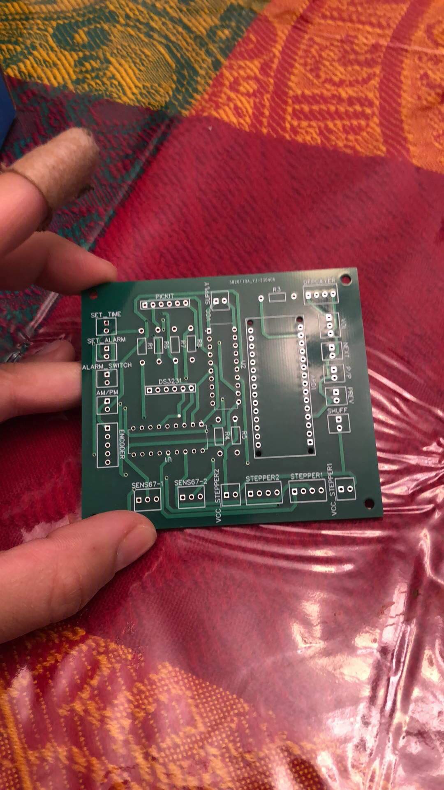
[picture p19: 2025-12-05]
Media/PCB Board.jpg

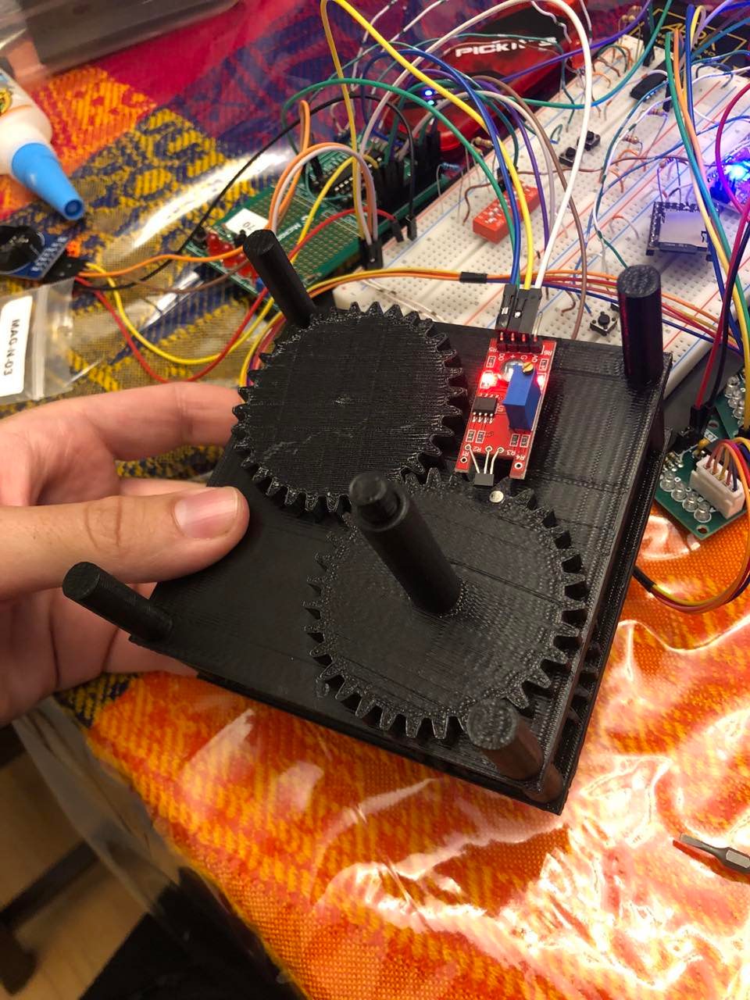
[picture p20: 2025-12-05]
Media/Gearbox.jpg

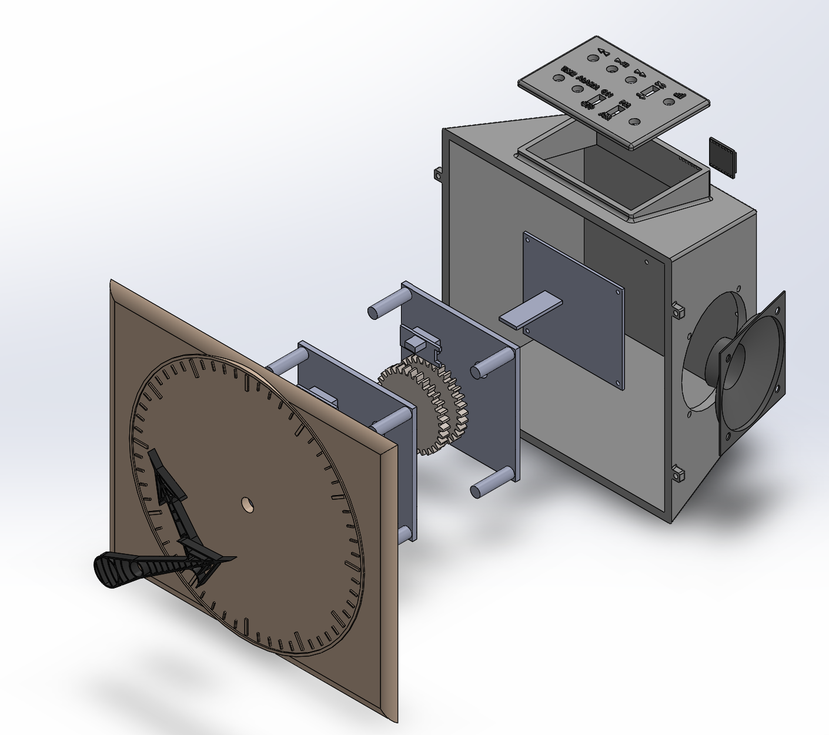
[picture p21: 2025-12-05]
Media/Clock_Exploded View1.png

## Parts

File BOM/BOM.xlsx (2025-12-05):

# | Name of Product | Part # | Quantity | Unity Cost | Cost | Source | Datasheet/Info
1 | Stepper Motor (With Driver Board) | MOT-28BYJ48 | 2 | $6.95 | $13.90 | Electromechanical :: Motors :: Stepper Motors :: Mini Stepper Motors :: MOT-28BYJ48 Stepper Motor w/ ULN2003 Driver (abra-electronics.com) (https://abra-electronics.com/electromechanical/motors/stepper-motors/mini-stepper-motors/mot-28byj48-stepper-motor-w-uln2003-driver.html)
2 | PIC Microcontroller | PIC16F690-I/P | 1 | $4.54 | $4.54 | PIC16F690-I/P IC,PIC16F690-I/P,PDIP-20,7K FL 256B RAM,8b MCU,18 I/O,20MHz (abra-electronics.com) (https://abra-electronics.com/ics-semiconductors/microcontrollers-pic/pic16f690-i-p-icpic16f690-i-ppdip-207k-fl-256b-ram8b-mcu18-i-o20mhz-pic16f690-i-p.html) | https://ww1.microchip.com/downloads/en/devicedoc/41262a.pdf
3 | RTC Module | ARD-DS3231 | 1 | $8.79 | $8.79 | Super Accurate Real Time Clock DS3231 AT24C32 (abra-electronics.com) (https://abra-electronics.com/robotics-embedded-electronics/breakout-boards/clocks/ard-ds3231-super-accurate-real-time-clock-ds3231.html) | https://www.analog.com/media/en/technical-documentation/data-sheets/ds3231.pdf
4 | Rotary Encoder | SW-ENC-03 | 1 | $4.38 | $4.38 | Digital Rotatory Potentiometer Module for Arduino (abra-electronics.com) (https://abra-electronics.com/passive-components/potentiometers/digital-potentiometers/digital-rotatory-potentiometer-module-for-arduino.html)
5 | Arduino Nano Board | ABRANANO | 1 | $19.45 | $19.45 | ABRA Arduino Nano V3.0 Compatible- ATmega328P (abra-electronics.com) (https://abra-electronics.com/robotics-embedded-electronics/arduino-boards/abranano-abra-arduino-nano-v3.0-compatible-atmega328p.html)
6 | Magnetic Hall Effect Sensor | SENS-67 | 2 | $2.79 | $5.58 | Linear Hall Magnetic Module For Arduino (abra-electronics.com) (https://abra-electronics.com/sensors/sensors-magneto-en-2/sens-67-magnetic-hall-effect-sensor-for-5v-microcontrollers.html)
7 | DFPlayer - MP3 Player Module | DFR0299 | 1 | $15.31 | $15.31 | DFR0299 DFPlayer - A Mini MP3 Player (abra-electronics.com) (https://abra-electronics.com/robotics-embedded-electronics/arduino-shields/audio-video-game-shields/dfr0299-dfplayer-a-mini-mp3-player-dfr0299.html) | https://wiki.dfrobot.com/DFPlayer_Mini_SKU_DFR0299
8 | Round Magnets 3x3mm (20 Pack) | MAG-N-03 | 1 | $2.41 | $2.41
9 | Speaker - 4ohms 3 Watts | 1314-ADA | 1 | $3.76 | $3.76 | 1314-ADA Speaker - 3" Diameter - 4 Ohm 3 Watt (abra-electronics.com) (https://abra-electronics.com/electromechanical/audible-devices/speakers/1314-ada-speaker-3-diameter-4-ohm-3-watt-1314-ada.html)
10 | IC Socket 18 Pin | 18LP | 1 | $0.15 | $0.15 | 18LP Solder Tail Low Profile Socket - 18 Pins (abra-electronics.com) (https://abra-electronics.com/interconnects/sockets/standard-tin-low-profile-sockets/18lp-solder-tail-low-profile-socket-18-pins-18lp.html)
11 | IC Socket 20 Pin | 20LP | 1 | $0.16 | $0.16 | 20LP Solder Tail Low Profile Socket - 20 Pins (abra-electronics.com) (https://abra-electronics.com/interconnects/sockets/standard-tin-low-profile-sockets/20lp-solder-tail-low-profile-socket-20-pins-20lp.html)
12 | Slide Switch SPDT | SSW-110 | 3 | $0.60 | $1.80 | SSW-110 Solder Slide Switch SPDT On-On (abra-electronics.com) (https://abra-electronics.com/electromechanical/switches/slide-switches/ssw-110-slide-switch-spdt-on-on-solder-tabs.html)
13 | Normal Open - Push Button | NO-112RD | 5 | $1.20 | $6.00 | Momentary Push Button Switch Red - Normally Open (abra-electronics.com) (https://abra-electronics.com/electromechanical/switches/pushbutton-switches/momentary-push-button-switch-red-normally-open.html)
14 | 40 Pin Header | FH-1 | 1 | $1.07 | $1.07 | FH-1 Header, 1 row X 40 pins Straight Female Receptacle (abra-electronics.com) (https://abra-electronics.com/interconnects/connectors/headers/female/fh-1-header-1-row-x-40-pins-straight-female-receptacle.html)
15 | 2-Pin Terminal Block, 4 Pack | 2491P | 3 | $3.46 | $10.38 | Interconnects :: Terminals/Blocks/Barrier :: Terminal Blocks :: Screw Terminal Blocks :: 2491P Screw Terminal Block: 2-Pin, 0.1″ Pitch, Side Entry (4-Pack) (abra-electronics.com) (https://abra-electronics.com/interconnects/terminals-blocks-barrier/terminal-blocks/screw-terminal-blocks/2491p-screw-terminal-block-2-pin-0.1-pitch-side-entr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)
16 | 3-Pin Terminal Block, 3 Pack | 2492P | 1 | $3.84 | $3.84 | Interconnects :: Terminals/Blocks/Barrier :: Terminal Blocks :: Screw Terminal Blocks :: 2492P Screw Terminal Block: 3-Pin, 0.1″ Pitch, Side Entry (3-Pack) (abra-electronics.com) (https://abra-electronics.com/interconnects/terminals-blocks-barrier/terminal-blocks/screw-terminal-blocks/2492p-screw-terminal-block-3-pin-0.1-pitch-side-entr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)
17 | 4-Pin Terminal Block, 2 Pack | 2493P | 2 | $3.46 | $6.92 | Interconnects :: Terminals/Blocks/Barrier :: Terminal Blocks :: Screw Terminal Blocks :: 2493P Screw Terminal Block: 4-Pin, 0.1″ Pitch, Side Entry (2-Pack) (abra-electronics.com) (https://abra-electronics.com/interconnects/terminals-blocks-barrier/terminal-blocks/screw-terminal-blocks/2493p-screw-terminal-block-4-pin-0.1-pitch-side-entr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)
18 | 5-Pin Terminal Block, 2 Pack | 2494P | 1 | $4.23 | $4.23 | Interconnects :: Terminals/Blocks/Barrier :: Terminal Blocks :: Screw Terminal Blocks :: 2494P Screw Terminal Block: 5-Pin, 0.1″ Pitch, Side Entry (2-Pack) (abra-electronics.com) (https://abra-electronics.com/interconnects/terminals-blocks-barrier/terminal-blocks/screw-terminal-blocks/2494p-screw-terminal-block-5-pin-0.1-pitch-side-entr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)
19 | PCB | Y3 | 1 | $18.38 | $18.38 | PCB Prototype & PCB Fabrication Manufacturer - JLCPCB (https://jlcpcb.com/)
 |  |  |  | Subtotal | $131.05
 |  |  |  | Total | $150.71

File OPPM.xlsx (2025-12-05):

Project 2, 244-586-AB, Analog Clock w/ alarm |  |  |  |  |  |  | Maya A. Rosales O.
Linking Tasks to Objectives |  |  |  |  | ID | Task Description | Status | January |  |  | February |  |  |  | March |  |  |  | April |  |  |  | May
 |  | 8 |  |  | T1 | Research (Initial) | D | ● | ●
 |  | 8 |  | 8 | T2 | Coding (Clock) | D |  | ● | ● | ● | ● | ● |  |  |  | ● | ● | ●
 | 8 |  |  | 8 | T3 | Analog Gear (Clock gearbox) | D |  |  |  |  |  |  |  |  |  | ● | ● |  | ● | ●
8 | 8 |  | 8 |  | T4 | 3D model | D |  |  |  | ● |  |  |  |  |  | ● |  |  | ● | ●
 |  | 8 |  |  | T5 | Coding (Music Player) | D |  |  |  |  |  |  |  |  |  |  | ● | ●
 |  |  | 8 |  | T6 | Print Board | D |  |  |  |  |  |  |  |  |  | ● |  |  | ● | ●
 |  | 8 | 8 |  | T7 | Wiring | D |  |  |  |  |  |  |  |  |  | ● |  |  |  | ●
8 | 8 | 8 |  |  | T8 | Case | D |  |  |  |  |  |  |  |  |  |  |  |  | ● | ●
8 |  |  |  |  | T9 | Engraving & Staining | D |  |  |  |  |  |  |  |  |  |  |  |  |  | ● | ●
8 |  | 8 | 8 | 8 | T10 | Final Assembly | D |  |  |  |  |  |  |  |  |  |  |  |  |  | ● | ●
 |  |  | 8 | 8 | T11 | Troubleshooting | D |  |  |  |  |  |  | ● | ● |  |  |  |  |  |  |  | ●
 |  |  | 8 |  | T12 | Continuous Updating | D |  |  |  |  |  |  |  |  |  |  | ● | ● |  |  |  | ● | ●
 |  |  | 8 | 8 | T13 | Continuous Research | D | ●
Linking KPIs to Objectives |  |  |  |  |  | Risks, Quantitatives, Other Metrics | Status
8 | 8 |  |  |  | KPIs | Noise
 |  | 8 |  | 8 |  | Reliability
8 | 8 | 8 | 8 |  |  | Aesthetics
8 | 8 |  |  |  |  | Size
8 |  |  | 8 | 8 |  | Cost
KEY OBJECTIVES
Aesthetically Pleasant Clock | Keep Clock's size relatively Small | Intuitive Usage | Keeping Low cost | Precision (resolution) & Reliability |  |  |  | 2023-01-16 | 2023-01-23 | 2023-01-30 | 2023-02-06 | 2023-02-13 | 2023-02-20 | 2023-02-27 | 2023-03-06 | 2023-03-13 | 2023-03-20 | 2023-03-27 | 2023-04-03 | 2023-04-10 | 2023-04-17 | 2023-04-24 | 2023-05-01 | 2023-05-08
 |  |  |  |  |  |  |  |  | UNPLANNED | O |  | CHECKING | C |  | MILESTONE | ◊
 |  |  |  |  |  |  |  |  | PLANNING | P |  | DONE | A |  | PLANNED | ○
 |  |  |  |  |  |  |  |  | DOING | D |  | Link symbol: | 8 |  | COMPLETED | ●
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

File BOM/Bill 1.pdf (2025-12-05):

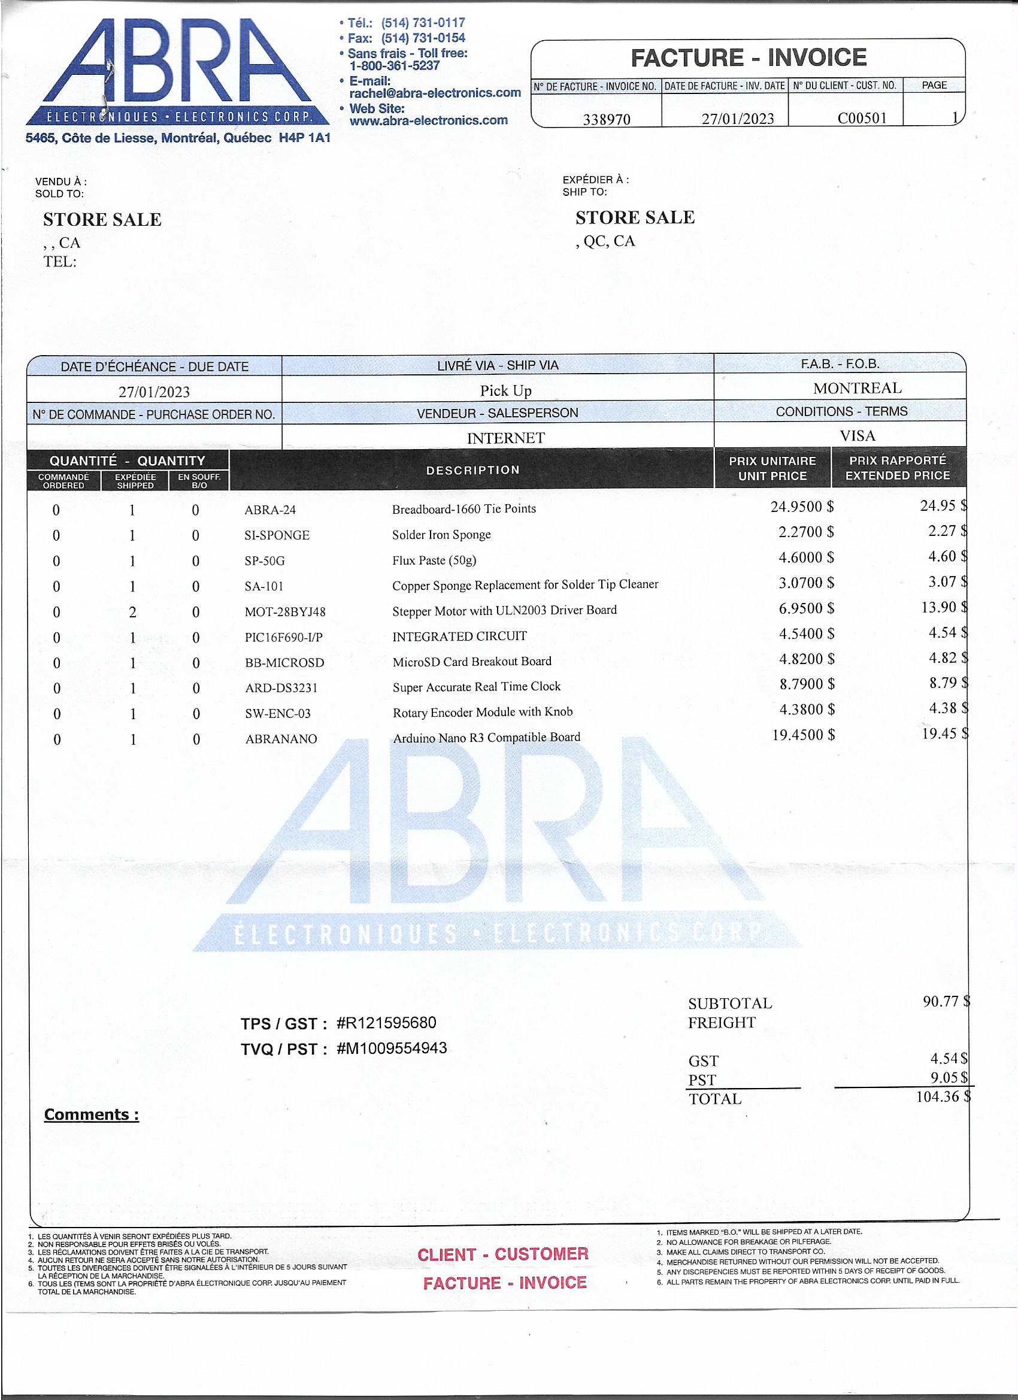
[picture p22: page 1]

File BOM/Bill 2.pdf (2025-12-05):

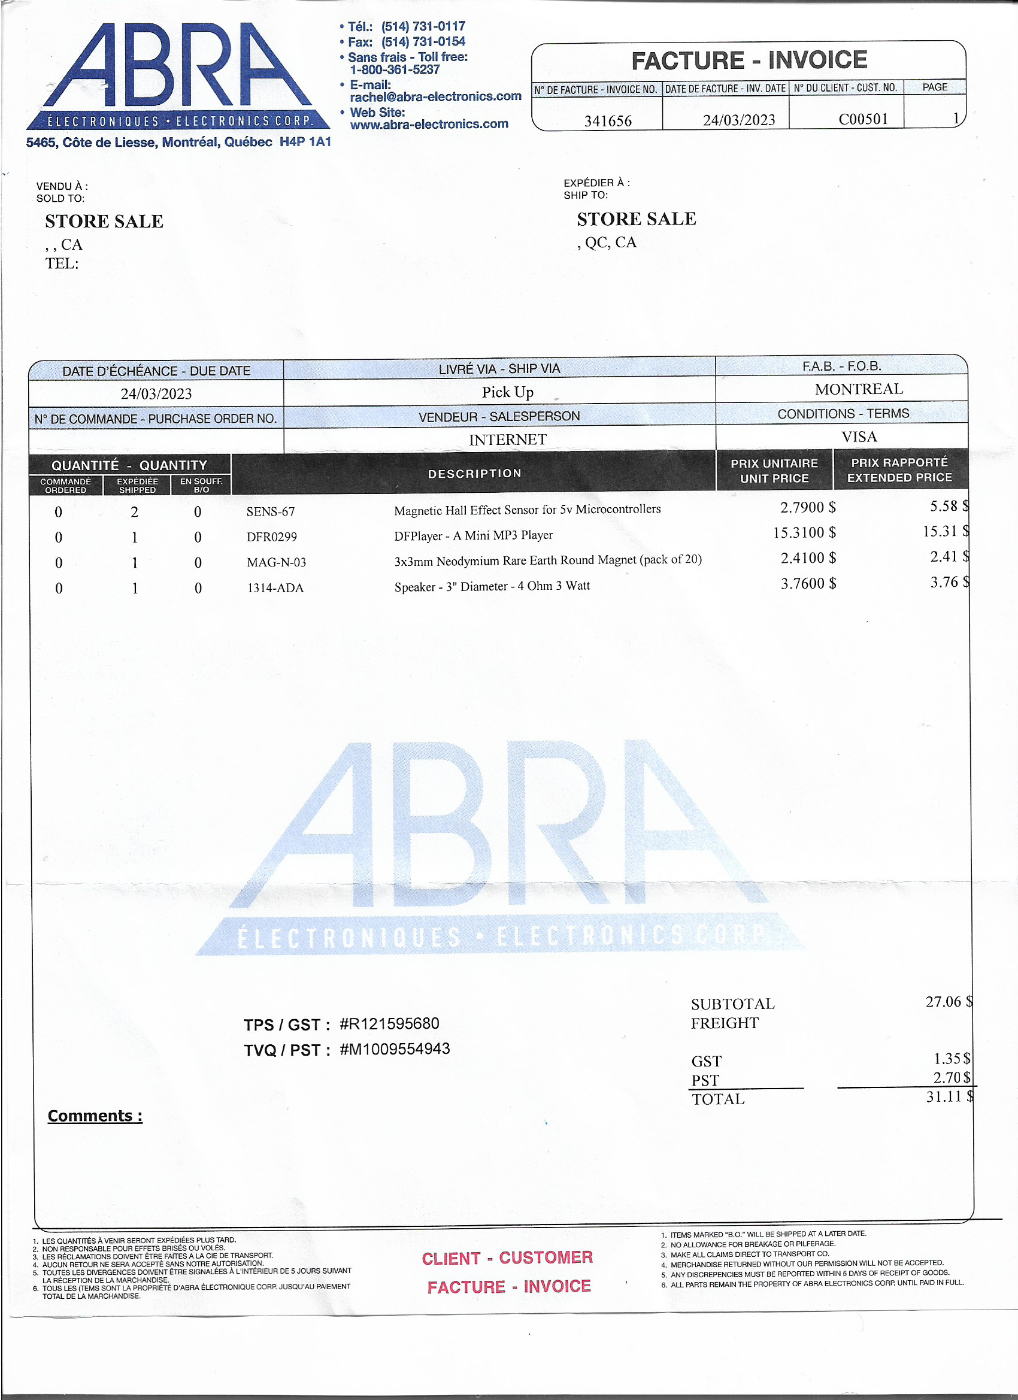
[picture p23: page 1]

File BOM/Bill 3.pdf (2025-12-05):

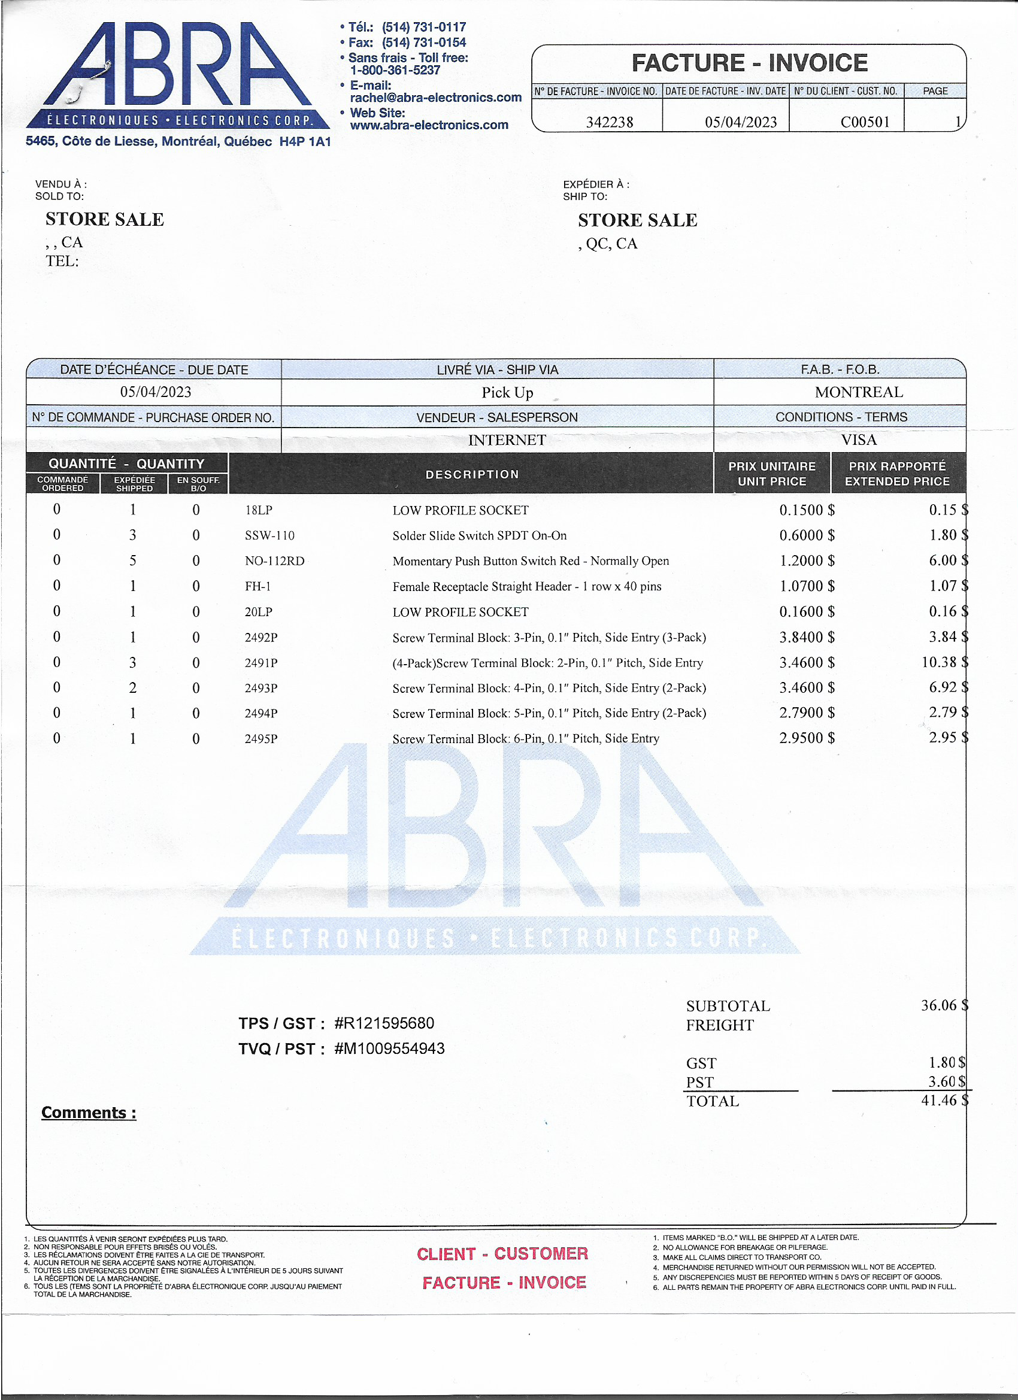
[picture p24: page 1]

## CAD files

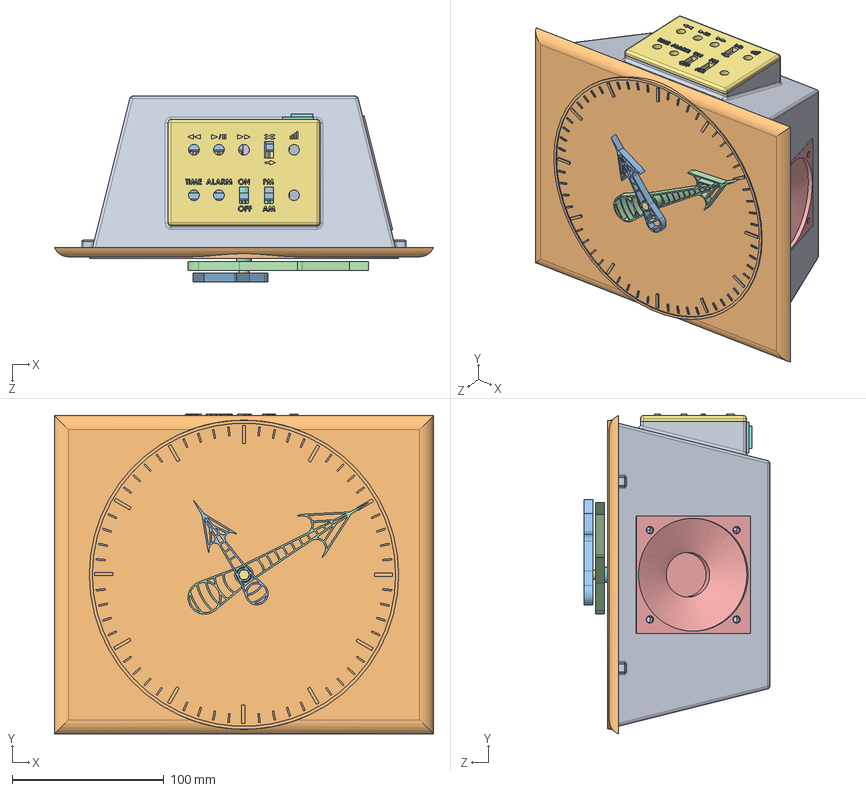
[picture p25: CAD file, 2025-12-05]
3D Model/Parts & Assembly/Clock.SLDASM
250.0 x 211.0 x 122.5 mm
Clock Case
Face Plate
Base Plate x 2
Reference - Motor x 2
Gear 32 x 2
Reference - Sensor x 2
Gear 32 - Inner
Gear 32 - Outter
Top Plate
Reference - Magnet x 2
Needle - Hours
Needle - Mins
Reference - Speaker
Reference - PCB
Control Plate V2
Reference - DFPlayer

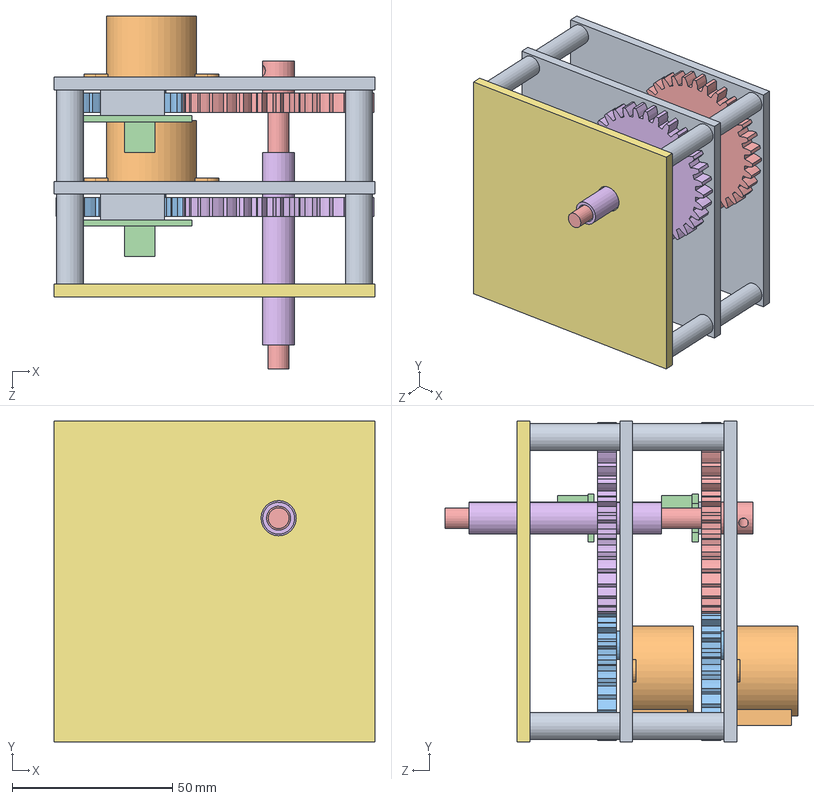
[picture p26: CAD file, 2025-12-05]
3D Model/Parts & Assembly/Gearbox/Gearbox.SLDASM
100.0 x 100.0 x 110.0 mm
Base Plate x 2
Reference - Motor x 2
Gear 32 x 2
Reference - Sensor x 2
Gear 32 - Inner
Gear 32 - Outter
Top Plate
Reference - Magnet x 2

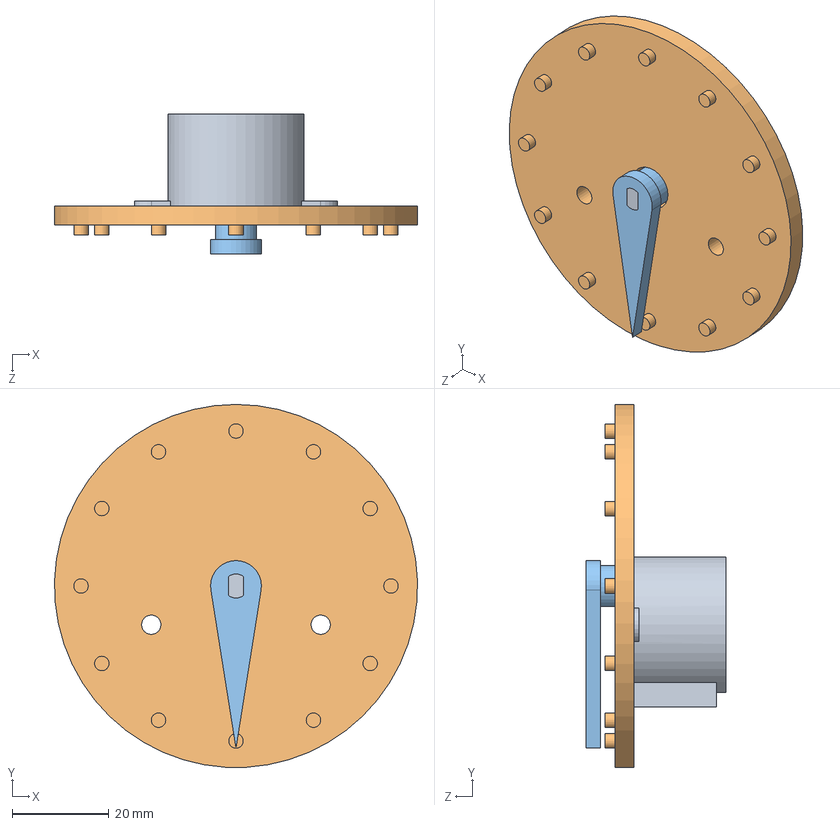
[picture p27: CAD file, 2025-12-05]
3D Model/Parts & Assembly/Misc/Simple Test/Simple Test.SLDASM
75.0 x 75.0 x 29.0 mm
Reference - Motor
Wall
Clock Needle

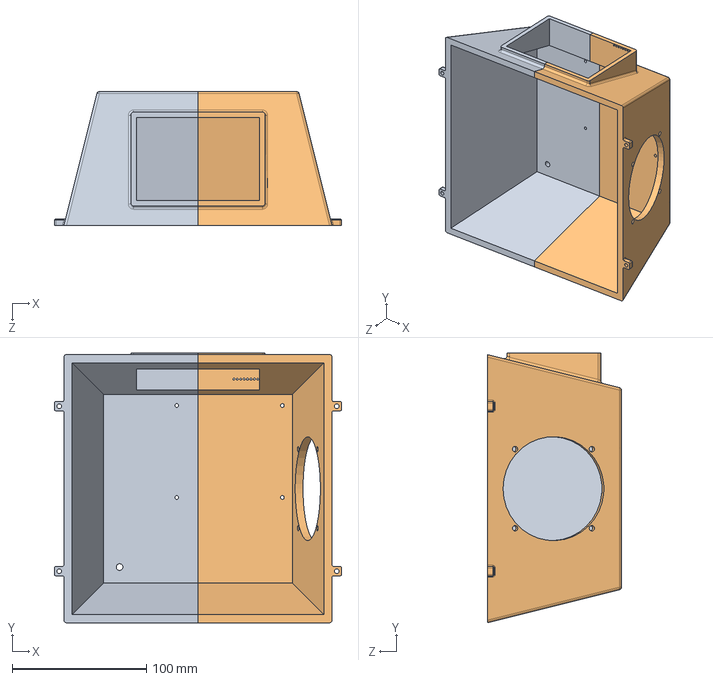
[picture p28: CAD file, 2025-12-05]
3D Model/STL/Print Case/Box Print Two Part.SLDASM
214.0 x 201.0 x 100.0 mm
Clock Case P1
Clock Case P2

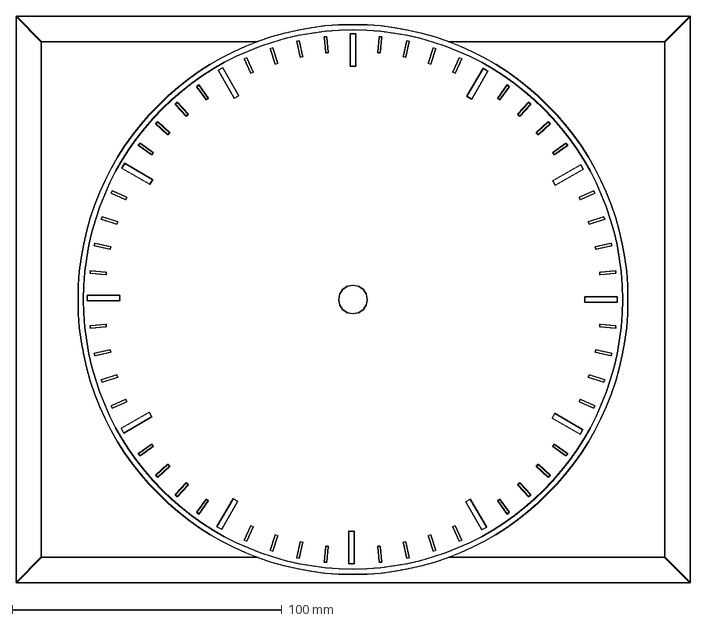
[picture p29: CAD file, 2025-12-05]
3D Model/DXF/Face Plate CND P1.DXF
250.0 x 210.0 mm

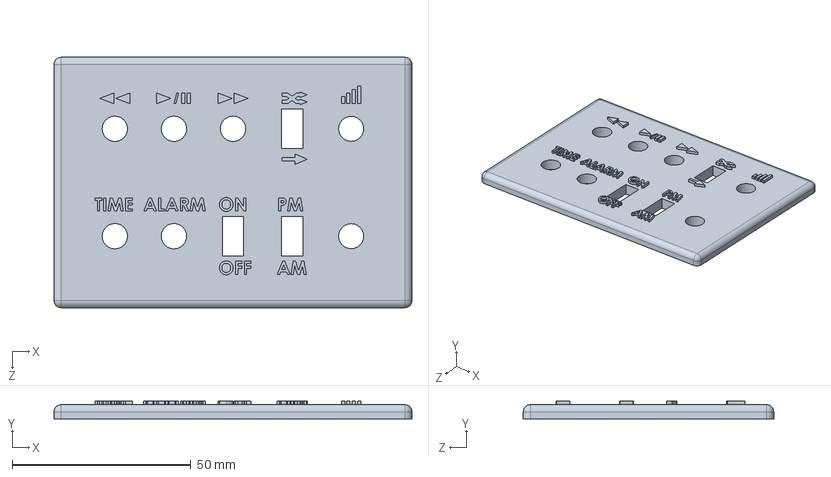
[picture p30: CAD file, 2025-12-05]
3D Model/Parts & Assembly/Clock Parts/Control Plate V2.SLDPRT
100.0 x 5.00 x 70.0 mm

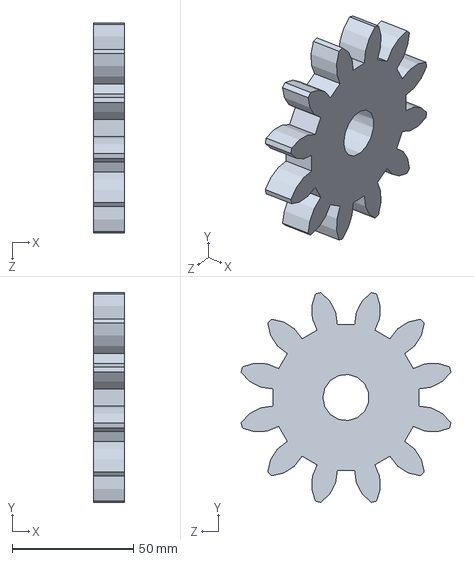
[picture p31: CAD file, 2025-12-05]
3D Model/Parts & Assembly/Gearbox/Gears/Gear 32.SLDPRT
12.7 x 86.4 x 86.4 mm

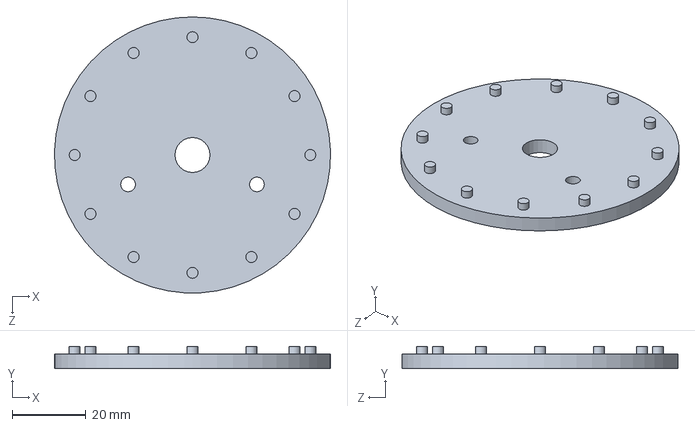
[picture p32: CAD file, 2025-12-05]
3D Model/Parts & Assembly/Misc/Simple Test/Wall.SLDPRT
75.0 x 6.00 x 75.0 mm

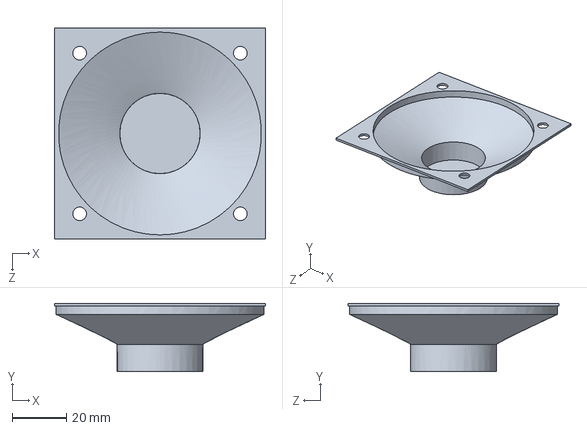
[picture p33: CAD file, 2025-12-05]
3D Model/Parts & Assembly/References/Reference - Speaker.SLDPRT
77.5 x 25.0 x 77.5 mm

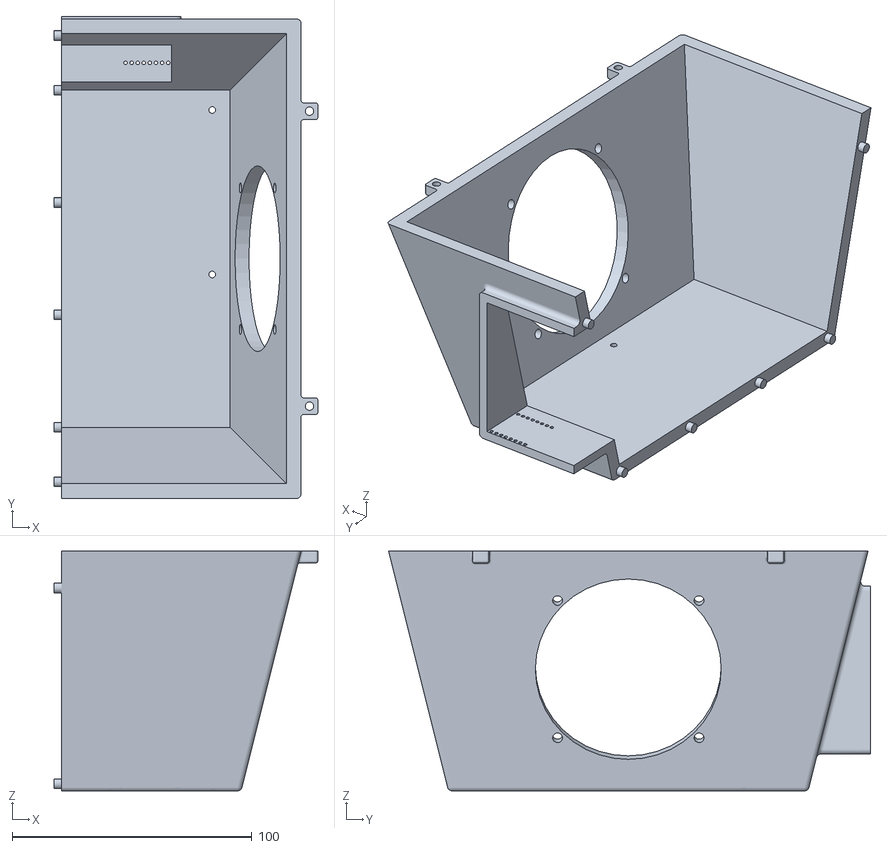
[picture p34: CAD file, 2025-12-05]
3D Model/STL/Clock Part2.STL
110.0 x 201.0 x 100.0

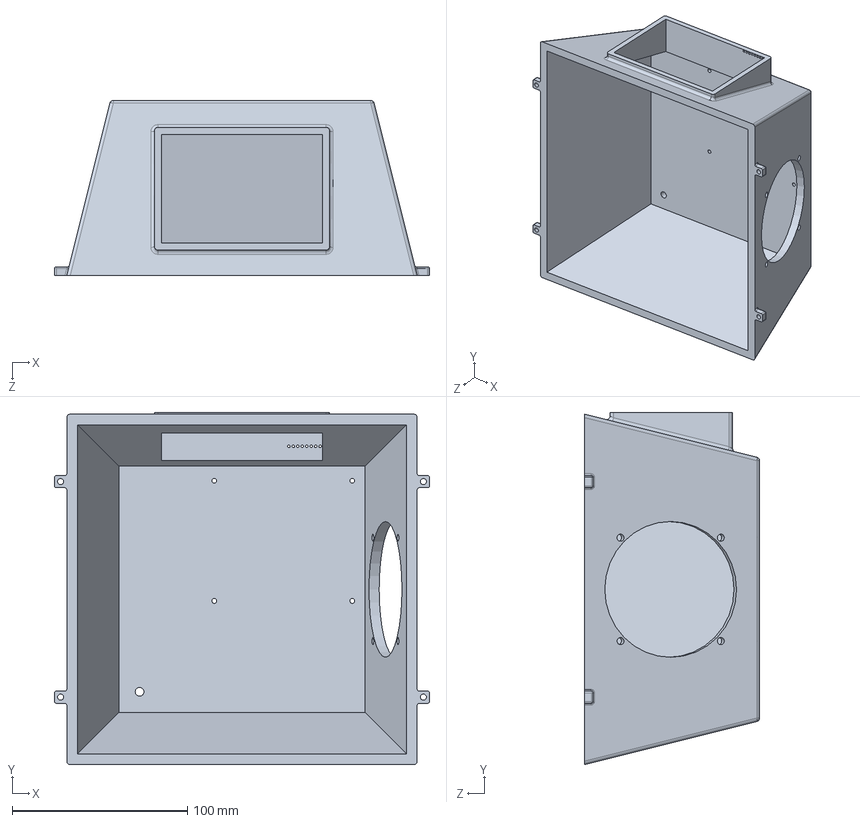
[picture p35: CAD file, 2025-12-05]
3D Model/STL/Print Case/Clock Case P2.SLDPRT
214.0 x 201.0 x 100.0 mm

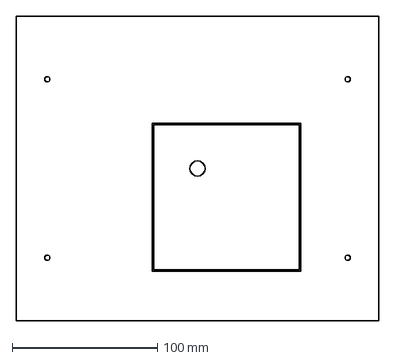
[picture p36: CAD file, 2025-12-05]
3D Model/DXF/Face Plate CND P2.DXF
250.0 x 210.0 mm

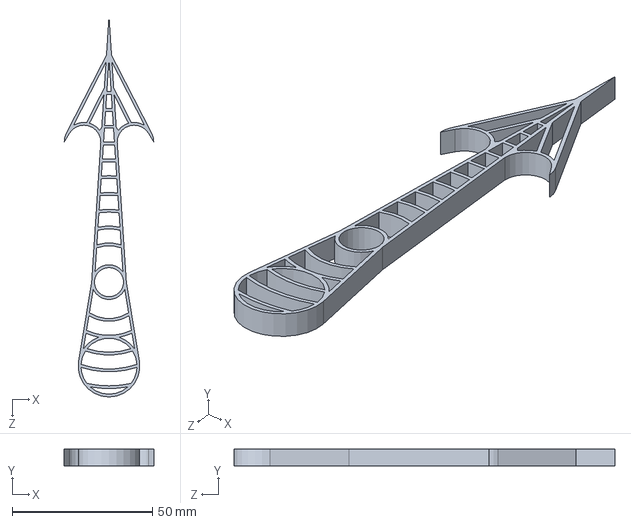
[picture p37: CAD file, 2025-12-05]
3D Model/Parts & Assembly/Clock Parts/Needle - Mins.SLDPRT
32.0 x 6.00 x 136.0 mm

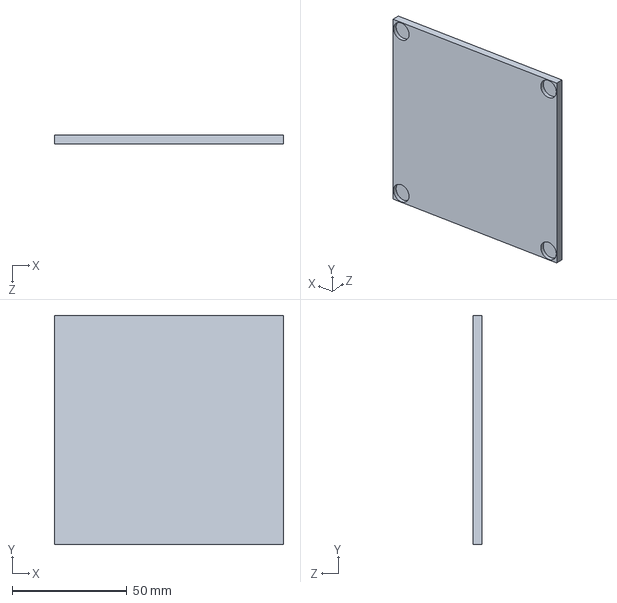
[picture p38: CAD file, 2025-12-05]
3D Model/Parts & Assembly/Gearbox/Top Plate.SLDPRT
100.0 x 100.0 x 4.00 mm

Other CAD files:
3D Model/Parts & Assembly/Gearbox/Gears/Gear 32 - Inner.SLDPRT
3D Model/Parts & Assembly/References/Reference - Motor.SLDPRT
3D Model/STL/Needle - Hours.STL
3D Model/STL/Print Case/Clock Case P1.SLDPRT
3D Model/DXF/Needle - Hours.DXF
3D Model/DXF/Needle - Mins.DXF
3D Model/Drawings/Technical Sheet/Maya A. Rosales O._P2_Clock Case.SLDDRW
3D Model/Drawings/Technical Sheet/Maya A. Rosales O._P2_Control Plate.SLDDRW
3D Model/Drawings/Technical Sheet/Maya A. Rosales O._P2_Gear Base.SLDDRW
3D Model/Drawings/Technical Sheet/Maya A. Rosales O._P2_Inner Gear.SLDDRW
3D Model/Drawings/Technical Sheet/Maya A. Rosales O._P2_Motor Gear.SLDDRW
3D Model/Drawings/Technical Sheet/Maya A. Rosales O._P2_Needle - Hour.SLDDRW
3D Model/Drawings/Technical Sheet/Maya A. Rosales O._P2_Needle - Min.SLDDRW
3D Model/Drawings/Technical Sheet/Maya A. Rosales O._P2_Outter Gear.SLDDRW
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

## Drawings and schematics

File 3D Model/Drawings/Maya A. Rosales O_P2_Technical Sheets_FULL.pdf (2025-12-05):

B

B

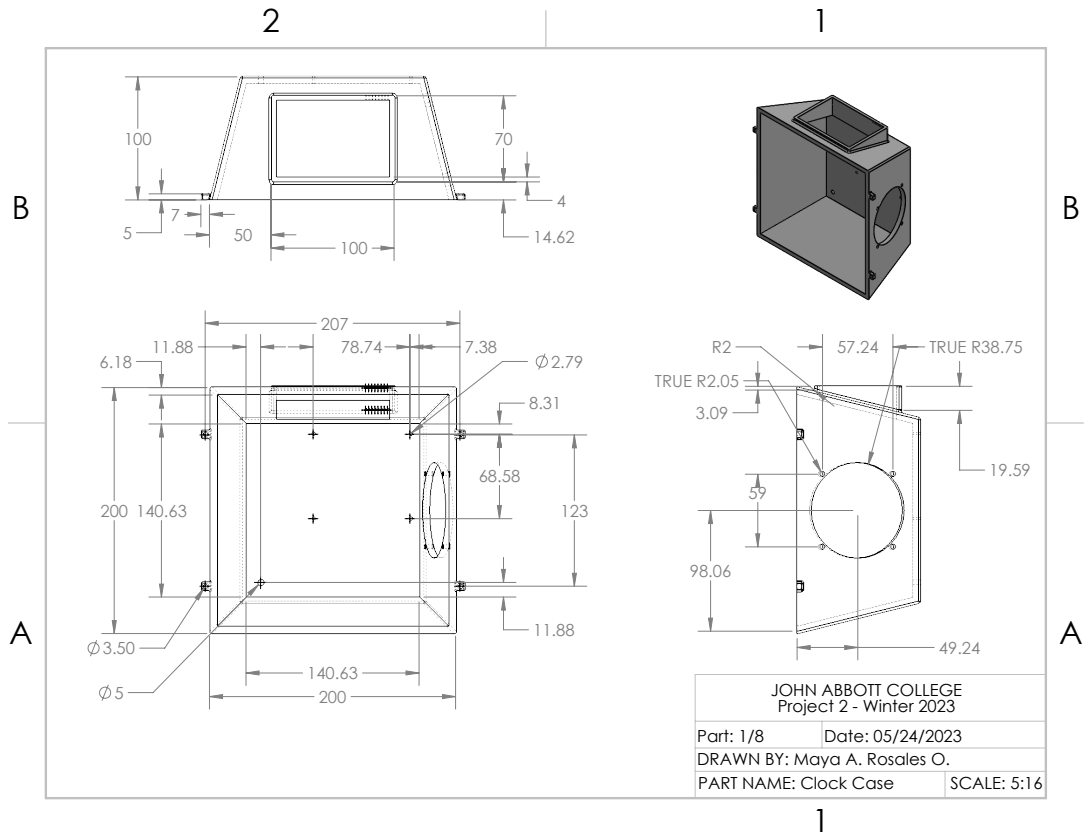
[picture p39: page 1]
TRUE R2.05; TRUE R38.75; Part: 1/8; Date: 05/24/2023; PART NAME: Clock Case; SCALE: 5:16

JOHN ABBOTT COLLEGE
Project 2 - Winter 2023

DRAWN BY: Maya A. Rosales O.

B

B

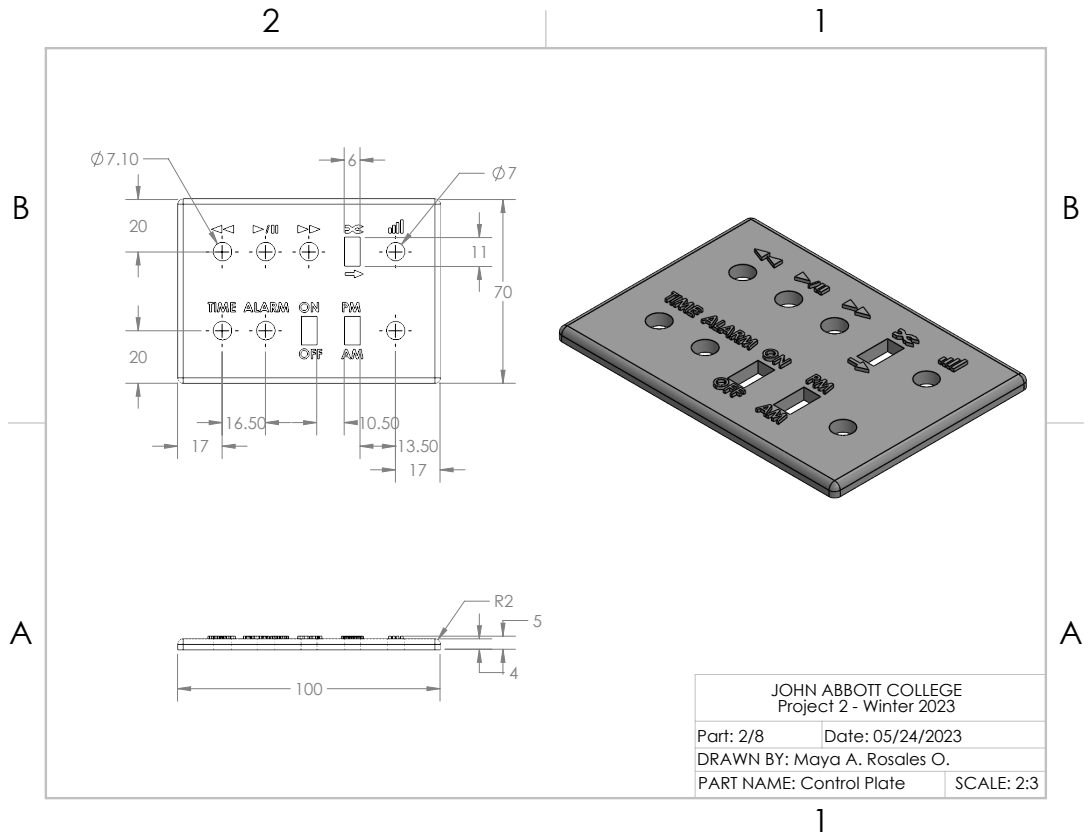
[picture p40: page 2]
Part: 2/8; Date: 05/24/2023; PART NAME: Control Plate; SCALE: 2:3

JOHN ABBOTT COLLEGE
Project 2 - Winter 2023

DRAWN BY: Maya A. Rosales O.

B

B

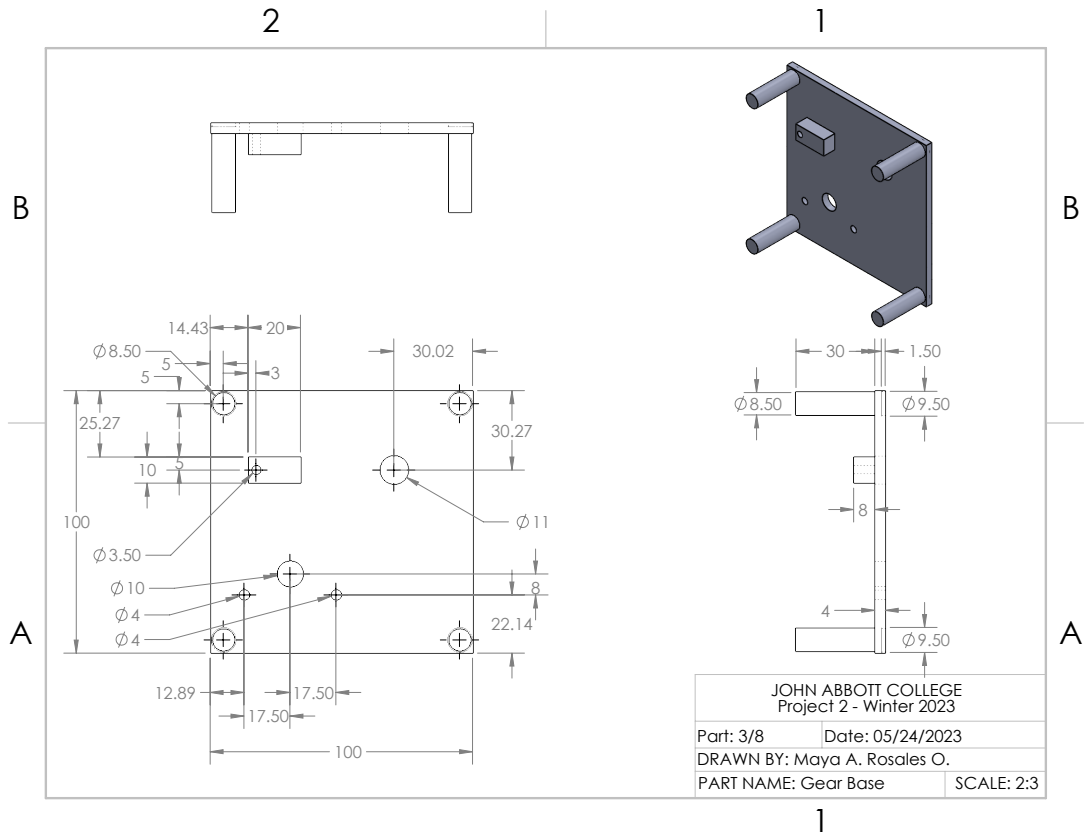
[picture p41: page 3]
Part: 3/8; Date: 05/24/2023; PART NAME: Gear Base; SCALE: 2:3

JOHN ABBOTT COLLEGE
Project 2 - Winter 2023

DRAWN BY: Maya A. Rosales O.

B

B

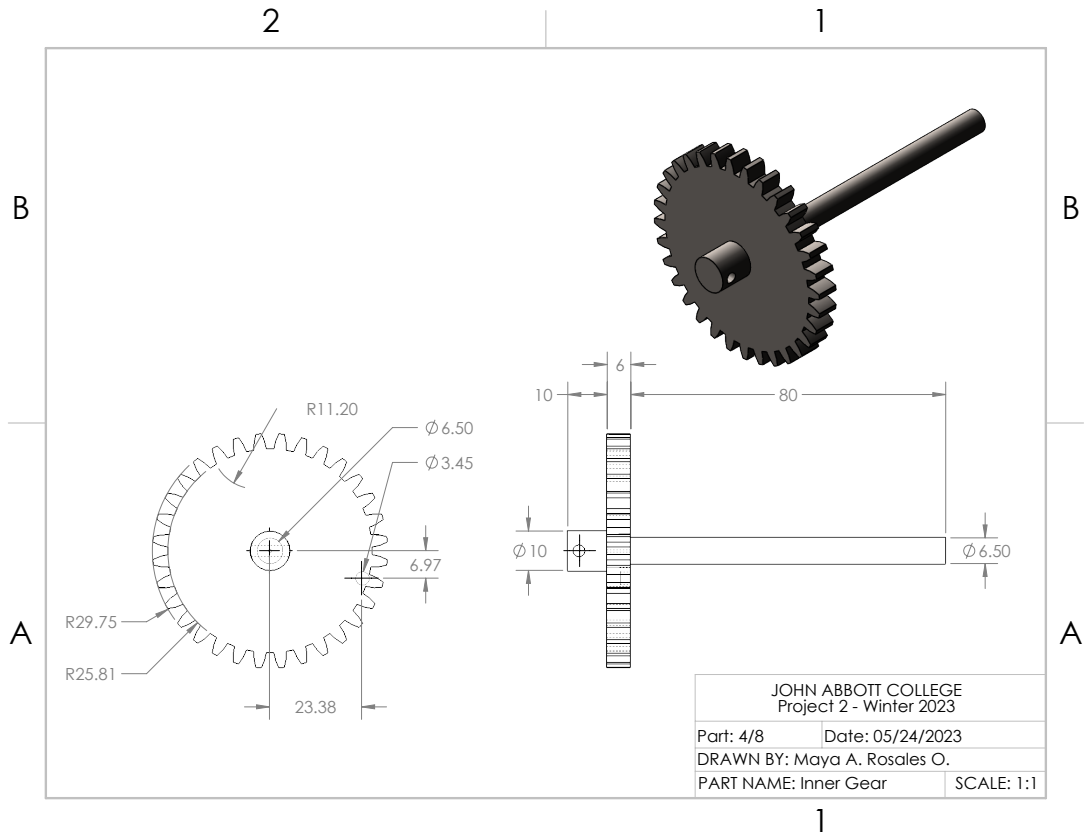
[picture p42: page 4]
Part: 4/8; Date: 05/24/2023; PART NAME: Inner Gear; SCALE: 1:1

JOHN ABBOTT COLLEGE
Project 2 - Winter 2023

DRAWN BY: Maya A. Rosales O.

B

B

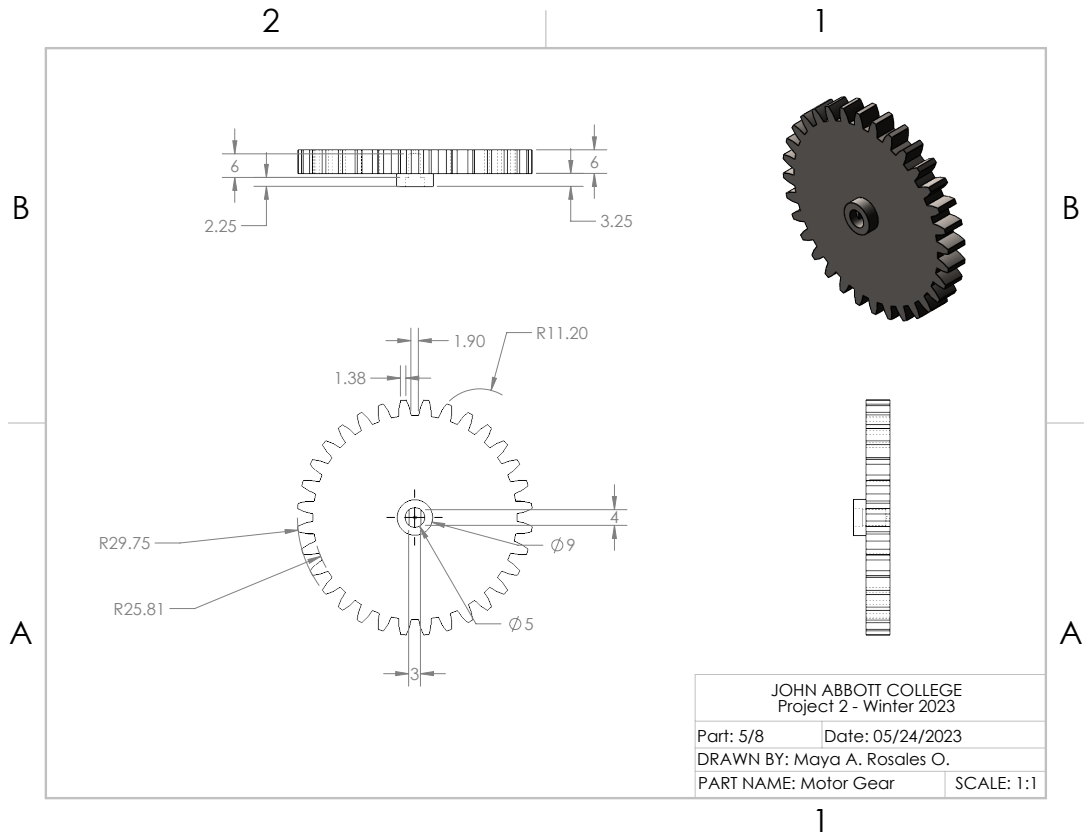
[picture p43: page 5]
Part: 5/8; Date: 05/24/2023; PART NAME: Motor Gear; SCALE: 1:1

JOHN ABBOTT COLLEGE
Project 2 - Winter 2023

DRAWN BY: Maya A. Rosales O.

B

B

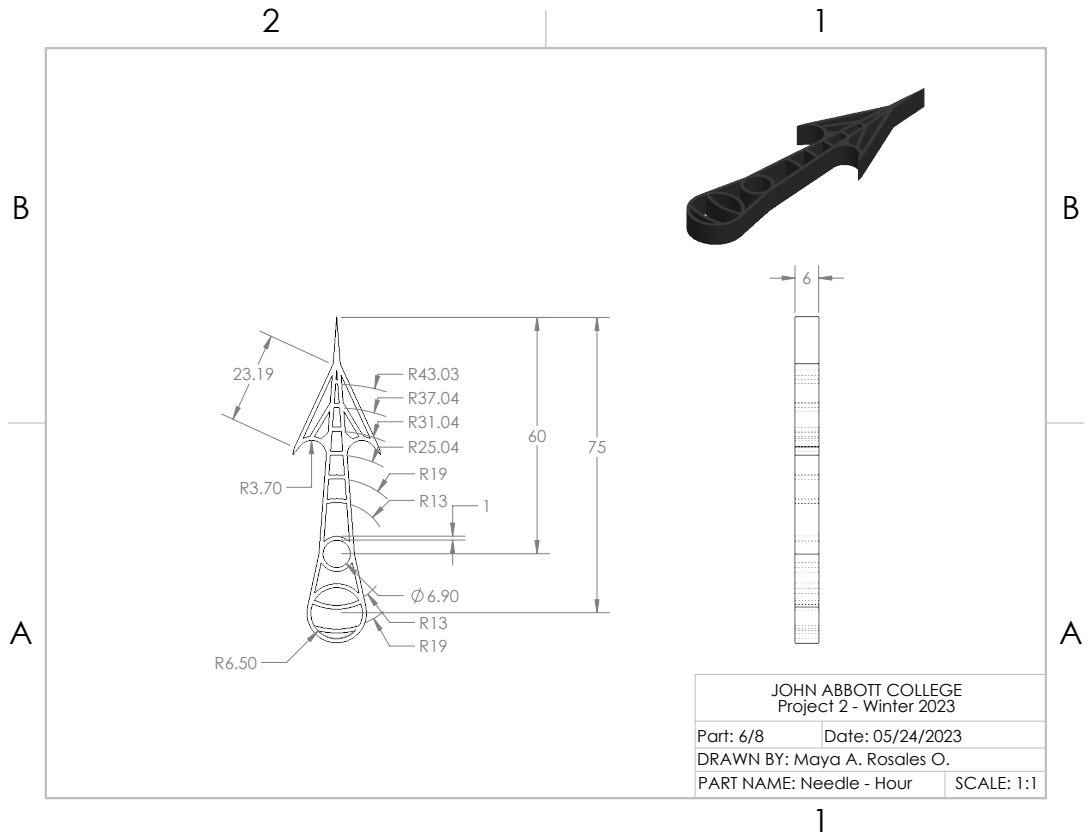
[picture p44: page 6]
Part: 6/8; Date: 05/24/2023; PART NAME: Needle - Hour; SCALE: 1:1

JOHN ABBOTT COLLEGE
Project 2 - Winter 2023

DRAWN BY: Maya A. Rosales O.

B

B

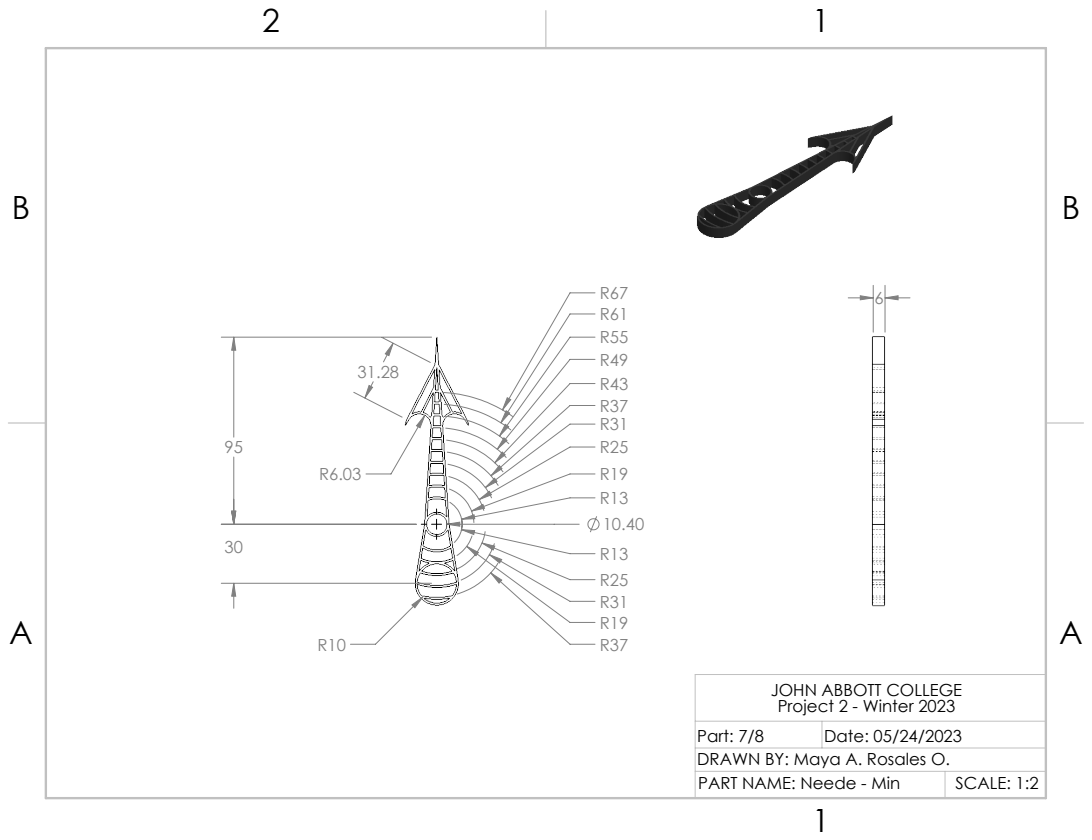
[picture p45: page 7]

DRAWN BY: Maya A. Rosales O.

B

B

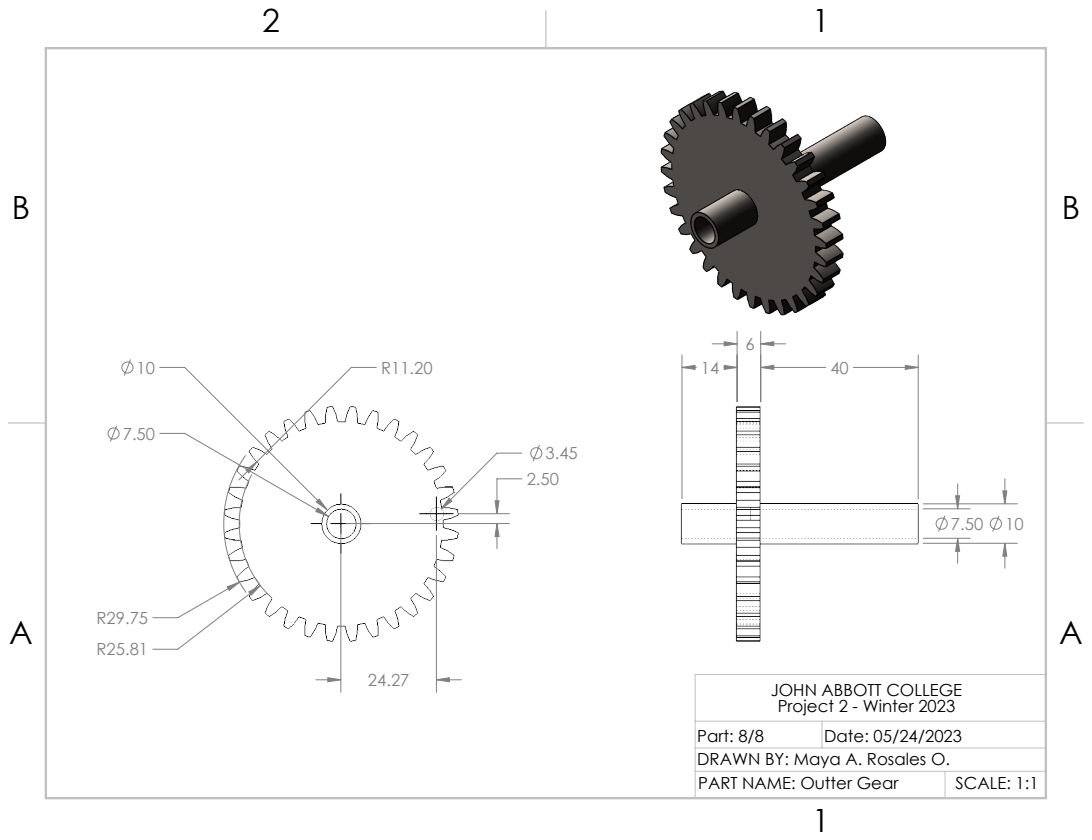
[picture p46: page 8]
Part: 8/8; Date: 05/24/2023; PART NAME: Outter Gear; SCALE: 1:1

JOHN ABBOTT COLLEGE
Project 2 - Winter 2023

DRAWN BY: Maya A. Rosales O.

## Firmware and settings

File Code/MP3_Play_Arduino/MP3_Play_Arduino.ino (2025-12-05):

#include <SoftwareSerial.h>

#include <DFRobotDFPlayerMini.h>

SoftwareSerial mySoftwareSerial(10, 11); // RX, TX
DFRobotDFPlayerMini myDFPlayer;
void printDetail(uint8_t type, int value);

int Play;     

int16_t Track;
int16_t Max_Track;

int volumeflag;
int volume;

int CardStatus;

int Shuffle;
int16_t ShuffleTrack;
int16_t ShuffledSongs[500];

int AlarmStat;

//Fix play status when previous/next

void setup() {
  // put your setup code here, to run once:
  mySoftwareSerial.begin(9600);
  Serial.begin(115200);

  pinMode(A2, INPUT);       // ADC Volume    
  
  pinMode(4, INPUT_PULLUP); // Shuffle Switch
  
  pinMode(6, INPUT_PULLUP); // set arduino pin to input pull-up mode Previous track
  pinMode(7, INPUT_PULLUP); // set arduino pin to input pull-up mode Pause/Play
  pinMode(8, INPUT_PULLUP); // set arduino pin to input pull-up mode Next Track
   
  pinMode(2, INPUT);        // Interrupt Pin for Alarm
  attachInterrupt(digitalPinToInterrupt(2), Alarm, FALLING);

  Serial.println();
  Serial.println(F("DFRobot DFPlayer Mini Demo"));
  Serial.println(F("Initializing DFPlayer ... (May take 3~5 seconds)"));

  if (!myDFPlayer.begin(mySoftwareSerial)) {  //Use softwareSerial to communicate with mp3.
    Serial.println(F("Unable to begin:"));
    Serial.println(F("1.Please recheck the connection!"));
    Serial.println(F("2.Please insert the SD card!"));
    
    while (true);
  }
  Serial.println(F("DFPlayer Mini online."));
  
  int volume=analogRead(A2);
  volume = volume/42.9;
  myDFPlayer.volume(volume);  
  int volumeflag=volume;
  
  Max_Track=myDFPlayer.readFileCounts();
  
  Track = 1;
  myDFPlayer.playMp3Folder(Track);
  delay(200);
  myDFPlayer.pause();
  
  Play=0;
  Shuffle= 0;
  CardStatus=1;
  AlarmStat=0;
}

void loop() {

  
  if (myDFPlayer.readType() == 2 && CardStatus != 1){ //if card is inserted. Reinitialize the MP3 player and checks the total number of songs
    delay(200);
    Max_Track=myDFPlayer.readFileCounts();
    
    Track = 1;
    myDFPlayer.playMp3Folder(Track); //play specific mp3 in SD:/MP3/0004.mp3; File Name(0~65535)();  //Play the first mp3
    delay(200);
    myDFPlayer.pause();
    
    Play=0;
    Shuffle= 0;
    CardStatus=1;
    Serial.println(Max_Track);
  }
  
  if (myDFPlayer.readType() == 3 && CardStatus != 0){ //if card is ejected CardStatus goes low
    CardStatus=0;
  }

  PausePlayVolume(); //Handles the Pause Play and Volume Function

  ShuffleCheck(); //Shuffles tracks

  PreviousNext(); //Auto Plays next song

  AutoPlay(); //Plays next song when current one finishes

  if(AlarmStat==1){
    if (Shuffle == 0){ 
      Track = 1;
      myDFPlayer.playMp3Folder(Track);
      Play = 1;
      Serial.println("Alarm (linnear)"); 
    }
  
    if (Shuffle == 1){
      Track = random(1, Max_Track); 
      myDFPlayer.playMp3Folder(Track);
      Play = 1;
      Shuffle = 0;
      Serial.println("Alarm (Shuffled)"); 
    }
    AlarmStat=0;
  }

  if (myDFPlayer.available()) {
    printDetail(myDFPlayer.readType(), myDFPlayer.read());
  }
}

void PausePlayVolume(void){
  //Pause Play//
  if(digitalRead(7) == LOW){
    Play=!Play;
    Serial.println("The button is pressed");
    
    if (Play==1){
      myDFPlayer.start();  //start the mp3 from the pause
      Serial.println("Music is playing");
    }
    if (Play==0){
      myDFPlayer.pause();  //pause the mp3
      Serial.println("Music is Paused");
    }
  
    delay(500);
  }
  //Volume
  volume=analogRead(A2); //Speaker can't handle a volume above 25. It starts crackling and the voltage drawn is high enough that it affects the voltage reference
  
  volume = volume/42.9; //Volume range is from 0 to 23.
  if(volumeflag != volume){
    Serial.println(volume);
    myDFPlayer.volume(volume);  
    volumeflag=volume;
  }
}

void ShuffleCheck (void){
  //Shuffle
  if(digitalRead(4)== HIGH && Shuffle != 1){ //If shuffle switch is HIGH and the songs haven't been shuffled before. 
    int16_t sum = 0;
    ShuffledSongs[0] = Track; //store in the 0 position of the array the current song being played. 
    for (int16_t i = 1; i < Max_Track ; i++) { //Generate an array with the rest of the number of song (eg. if Track 2 current being played, array = 2,1,3,4,5,...)
      sum++;
      if (sum == Track){
        sum++;
        ShuffledSongs[i] = sum;
      }
      else{
        ShuffledSongs[i] = sum;
      }
    }
    
    for (int16_t i=1; i < Max_Track; i++) { //Take previous array and shuffled by switching positions of the array at random N number of times)(N=max amount of songs in the array)
      int16_t n = random(1, Max_Track); //range between 1 and max songs because we don't want to affect the position array position 0. This is the song currently being played. 
      int16_t temp = ShuffledSongs[n];
      ShuffledSongs[n] =  ShuffledSongs[i];
      ShuffledSongs[i] = temp;
    }  
  Shuffle = 1; //Shuffle status is set to HIGH
  ShuffleTrack = 0; //Sets the current songs as the first song in the array. 
  Serial.println("Music Shuffled!");
  }
  //Unshuffle
  if(digitalRead(4)== LOW && Shuffle != 0){ //If the shuffle switch is LOW and the songs HAVE been shuffled.
    Track=ShuffledSongs[ShuffleTrack]; //Simply store the song currently being played as the Current Track
    Shuffle = 0; //Set shuffle status to LOW
    Serial.println("Linnear Play");
  }
}

void PreviousNext(void){
  //Previous track
    if(digitalRead(6) == LOW){ //if Previous button pressed
    if(Shuffle == 0){ //If unshuffled 
      if(Track == 1){Track = Max_Track;} //Check if we're at the first song and if so roll over. 
      else Track--; //If not play previous song
      myDFPlayer.playMp3Folder(Track); 
      Serial.println("Previous Track (Linear)");
      delay(500);   
    }
    if(Shuffle == 1){ //If shuffled
      if(ShuffleTrack == 0){ShuffleTrack = Max_Track-1;} //Check if we're at the first shuffled track and if so roll over. 
      else ShuffleTrack--; //if not play previous shuffled track
      myDFPlayer.playMp3Folder(ShuffledSongs[ShuffleTrack]);
      Serial.println("Previous Track (Shuffle)");
      delay(500); 
    }
    Play=1;
  }
  //Next track
  if(digitalRead(8) == LOW){ //same as Previous function but for the forwards instead of backwards. 
    if (Shuffle == 0){ 
      if(Track == Max_Track){Track=1;}
      else Track++;
      myDFPlayer.playMp3Folder(Track); 
      Serial.println("Next Track (Linnear)");
      delay(500);      
    }
    if (Shuffle == 1){ //Next track (Shuffled)
      if(ShuffleTrack == Max_Track-1){ShuffleTrack=0;}
      else ShuffleTrack++;
      myDFPlayer.playMp3Folder(ShuffledSongs[ShuffleTrack]);
      Serial.println("Next Track (Shuffle)");
      delay(500);  
    }
    Play=1;
  }
}

void AutoPlay(void){ //A copy of the Next Song function but with a different trigger. 
  if (myDFPlayer.readType() == 5){ 
    if (Shuffle == 0){ //Next track (Unshuffled)
      if(Track == Max_Track){Track=1;}
      else Track++;
      myDFPlayer.playMp3Folder(Track);
      Serial.println("Next Track (Linnear)");
    }
    if (Shuffle == 1){ //Next track (Shuffled)
      if(ShuffleTrack == Max_Track-1){ShuffleTrack=0;}
      else ShuffleTrack++;
      myDFPlayer.playMp3Folder(ShuffledSongs[ShuffleTrack]);
      Serial.println("Next Track (Shuffle)"); 
    }
  }
}

void Alarm(void){ //If alarm goes off, set alarm status to high 
  Serial.println("Alarm! Interrupt!"); 
  AlarmStat=1; 
}

void printDetail(uint8_t type, int value) {
  switch (type) {
    case TimeOut:
      Serial.println(F("Time Out!"));
      break;
    case WrongStack:
      Serial.println(F("Stack Wrong!"));
      break;
    case DFPlayerCardInserted:
      Serial.println(F("Card Inserted!"));
      break;
    case DFPlayerCardRemoved:
      Serial.println(F("Card Removed!"));
      break;
    case DFPlayerCardOnline:
      Serial.println(F("Card Online!"));
      break;
    case DFPlayerPlayFinished:
      Serial.print(F("Number:"));
      Serial.print(value);
      Serial.println(F(" Play Finished!"));
      break;
    case DFPlayerError:
      Serial.print(F("DFPlayerError:"));
      switch (value) {
        case Busy:
          Serial.println(F("Card not found"));
          break;
        case Sleeping:
          Serial.println(F("Sleeping"));
          break;
        case SerialWrongStack:
          Serial.println(F("Get Wrong Stack"));
          break;
        case CheckSumNotMatch:
          Serial.println(F("Check Sum Not Match"));
          break;
        case FileIndexOut:
          Serial.println(F("File Index Out of Bound"));
          break;
        case FileMismatch:
          Serial.println(F("Cannot Find File"));
          break;
        case Advertise:
          Serial.println(F("In Advertise"));
          break;
        default:
          break;
      }
      break;
    default:
      break;
  }
}

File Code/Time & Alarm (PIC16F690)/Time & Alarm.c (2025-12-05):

#include <Set_Time.h>
#include <DS3231.h>
#include <Stepper_Header_V2.h>
#Include <Steps_2_time.h>

#bit A2 = 0x05.2 //Encoder PB
#bit A4 = 0x05.4 //Encoder S2
#bit A5 = 0x05.5 //Encoder S1

#bit B4 = 0x06.4 //PB Adjust_Time_Tog
#bit B5 = 0x06.5 //PB Adjust_Alarm_Tog
#bit B6 = 0x06.6 //Hall Sensor
#bit B7 = 0x06.7 //Hall Sensor

#bit C0 = 0x07.0 //SWITCH Alarm ON/OFF
#bit C1 = 0x07.1 //SWITCH AM/PM
#bit C2 = 0x07.2 //Alarm INT
#bit C3 = 0x07.3 //
//#bit C4 = 0x07.4 //I2C MS23008 
//#bit C5 = 0x07.5 //I2C MS23008
//#bit C6 = 0x07.6 //I2C DS3231
//#bit C7 = 0x07.7 //I2C DS3231

int16 time_min;
int16 time_hr;

void Adjust_time(VOID);
void Adjust_Alarm(VOID);
void display_time(VOID);

void Buttons (VOID);

int Adjust_Time_tog;
int Adjust_Alarm_tog;
int Alarm_Stat;
int hr_or_min;

Void Alarm_Check(VOID);

Void Set_Zero(VOID);

#INT_RA
void  RA_isr(VOID) 
{
   IF (hr_or_min == 0)
   {
      IF (A4 == 1&&A5 == 1) S2_Setpoint += 17;
      IF (A4 == 0&&A5 == 1) S2_Setpoint -= 17; 
   }

   IF (hr_or_min == 1)
   {
      IF (A4 == 1&&A5 == 1) S1_Setpoint += 17;
      IF (A4 == 0&&A5 == 1) S1_Setpoint -= 17;
   }
}

void main()
{
   Enable_Steppers ();
   
   TRISA = 0xff;
   TRISB = 0xff;
   TRISC = 0XFF;
   
   enable_interrupts (GLOBAL);
   
   hr_or_min = 0;
   
   Adjust_Time_tog = 0;
   Adjust_Alarm_tog = 0;
   
   Alarm_status (Off);
   Alarm_Stat = 0;
   
   Set_Zero();
   
   WHILE (TRUE)
   {
      Buttons ();
      
      IF (Adjust_Time_tog == 1 && Adjust_Alarm_tog == 0)
      {
         enable_interrupts (INT_RA5);
         Adjust_time ();
      }
      
      else if (Adjust_Time_tog == 0 && Adjust_Alarm_tog == 1)
      {
         enable_interrupts (INT_RA5);
         Adjust_Alarm () ;
      }
     
      else if (Adjust_Time_tog == 0 && Adjust_Alarm_tog == 0)
      {
         disable_interrupts (INT_RA5);
         Display_time ();
      }

      ELSE
      {
         Adjust_Time_tog = 0;
         Adjust_Time_tog = 0;
      }
      
      Alarm_Check () ;
   }
}

void Adjust_time(VOID)
{
   IF (A2 == 0){hr_or_min = ! hr_or_min; delay_ms (100); }//Toggle Button
   Stepper1 (S1_Setpoint);
   Stepper2 (S2_Setpoint);
   Overflow_Protect ();
   IF (C1 == 1) Set_Time (Steps_2_hr (S2_Setpoint), Steps_2_min (S1_Setpoint), PM);
   IF (C1 == 0) Set_Time (Steps_2_hr (S2_Setpoint), Steps_2_min (S1_Setpoint), AM);
}

void display_time(VOID)
{
   //// Minutes and Stepper1 ////
   Time_min = Read_time_DEC (0x01);
   
   IF (Time_min == 0&&S1_Current_Pos != 1000)
   {
      Stepper1 (3048);
      S1_Current_Pos = 1000;
   }

   ELSE Stepper1 (Min_2_Steps (Time_min)) ;
   
   //// Hours and Stepper2 ////
   time_hr = (0x1F&Read_time_BCD (0x02));
   time_hr = BCD_2_DEC (time_hr);
   
   IF (Time_min == 0 && time_hr == 1 && S2_Current_Pos != 1170)
   {
      Stepper2 (3218);
      S2_Current_Pos = 1170;
   }

   ELSE Stepper2 (hours(time_hr, Time_min));
}

void Adjust_Alarm(VOID)
{
   IF (A2 == 0){hr_or_min = !hr_or_min; delay_ms (100); } //Toggle Button
   Stepper1 (S1_Setpoint);
   Stepper2 (S2_Setpoint);
   Overflow_Protect ();
   IF (C1 == 1) Set_Alarm (Steps_2_hr (S2_Setpoint), Steps_2_min (S1_Setpoint), PM);
   IF (C1 == 0) Set_Alarm (Steps_2_hr (S2_Setpoint), Steps_2_min (S1_Setpoint), AM);
}

void Buttons (VOID)
{
   IF (B4 == 0){Adjust_Time_tog = !Adjust_Time_tog; delay_ms (100); }
   IF (B5 == 0){Adjust_Alarm_tog = !Adjust_Alarm_tog; delay_ms (100); }
   
   IF (C0 == 1 && Adjust_Alarm_tog == 0 && Adjust_Time_tog == 0 && Alarm_Stat == 0){Clear_Alarm (); Alarm_status (ON); Alarm_Stat = 1; }
   //If C0 is high AND the time or alarm aren't being adjusted AND the alarm is't already on, Turn alarm on and change alarm status
   IF ((C0 == 0||Adjust_Alarm_tog == 1||Adjust_Time_tog == 1) && Alarm_Stat == 1){Alarm_status (OFF); Alarm_Stat = 0; }
   //If C0 is low OR the time or alarm is being adjusted AND the alarm isn't already off, Turn off alarm and change alarm status
}

Void Alarm_Check (VOID)
{
   IF (C2 == 0){Delay_ms (1000); Clear_Alarm (); }
}

Void Set_Zero (VOID)
{
   WHILE (B6 == 0){S1_Setpoint--; Stepper1 (S1_Setpoint);}
   WHILE (B6 == 1){S1_Setpoint++; Stepper1 (S1_Setpoint);}

   S1_Setpoint = 1000;
   S1_Current_Pos = 1000;
   
   WHILE (B7 == 0){S2_Setpoint--; Stepper2 (S2_Setpoint);}
   WHILE (B7 == 1){S2_Setpoint++; Stepper2 (S2_Setpoint);}
   
   S2_Setpoint = 1000;
   S2_Current_Pos = 1000;
}
